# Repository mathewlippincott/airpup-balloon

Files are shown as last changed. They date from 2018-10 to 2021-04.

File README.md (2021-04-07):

# the Airpup kite balloon
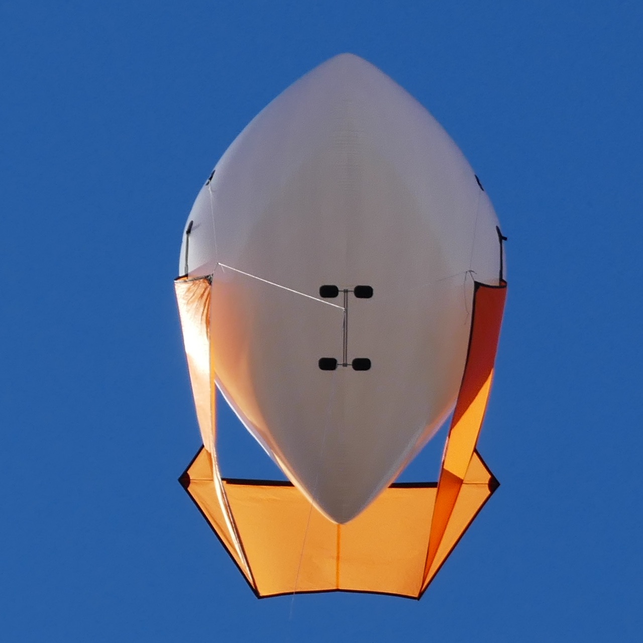
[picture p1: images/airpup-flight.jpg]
Airpup in flight
 

This repository contains the 2D patterns for constructing [Airpup](https://headfullofair.com/tags/airpup) as well as a corresponding 3D model. 2D patterns are made with [QCAD](https://qcad.org), the 3D model was made in Audodesk's Fusion 360.

See more of my kite and balloon projects at [headfullofair.com](https://headfullofair.com).

### files

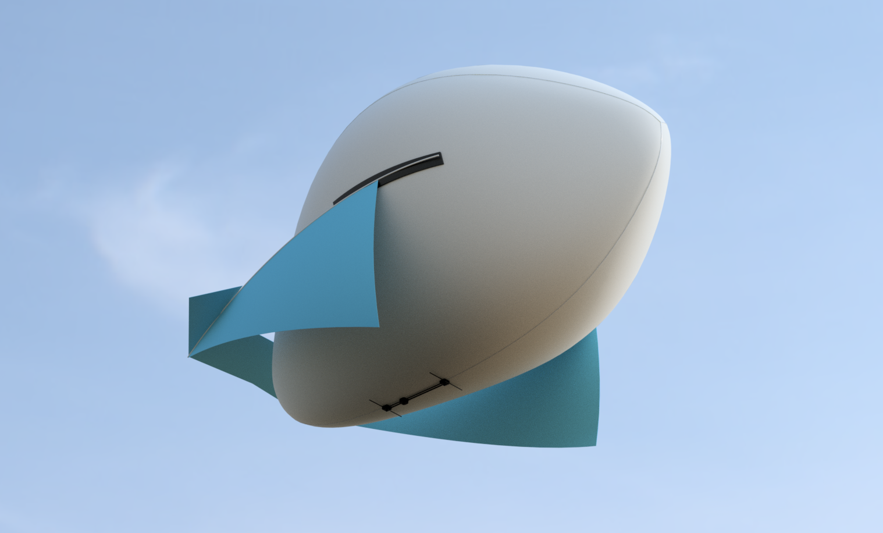
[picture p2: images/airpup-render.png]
rendering of airpup


* [/rails](rails), *belly mounting rails and STLs*
* BOM.ods, *Bill of Materials*
* V3-FIN.DXF, *panel diagram of the fin/wing structure and attachment*
* V3-ENVELOPE.DXF, *flat pattern of the balloon envelope*
* 72in-Airpup-model-v3.f3z/step/iges, *full-size 3D Airpup- Envelope is accurate in size, volume, and seam locations, fins are illustrative.*

Fin and envelope flat patterns have a series of rounded-rectanges that correspond to the glued interconnections joining the sewn fins and envelope. 

### sewing assembly
[airpup-assembly.md](airpup-assembly.md) contains instructions on sewing Airpup. 

### envelope construction

The envelope is a 3-gore pattern seamed in a single run:

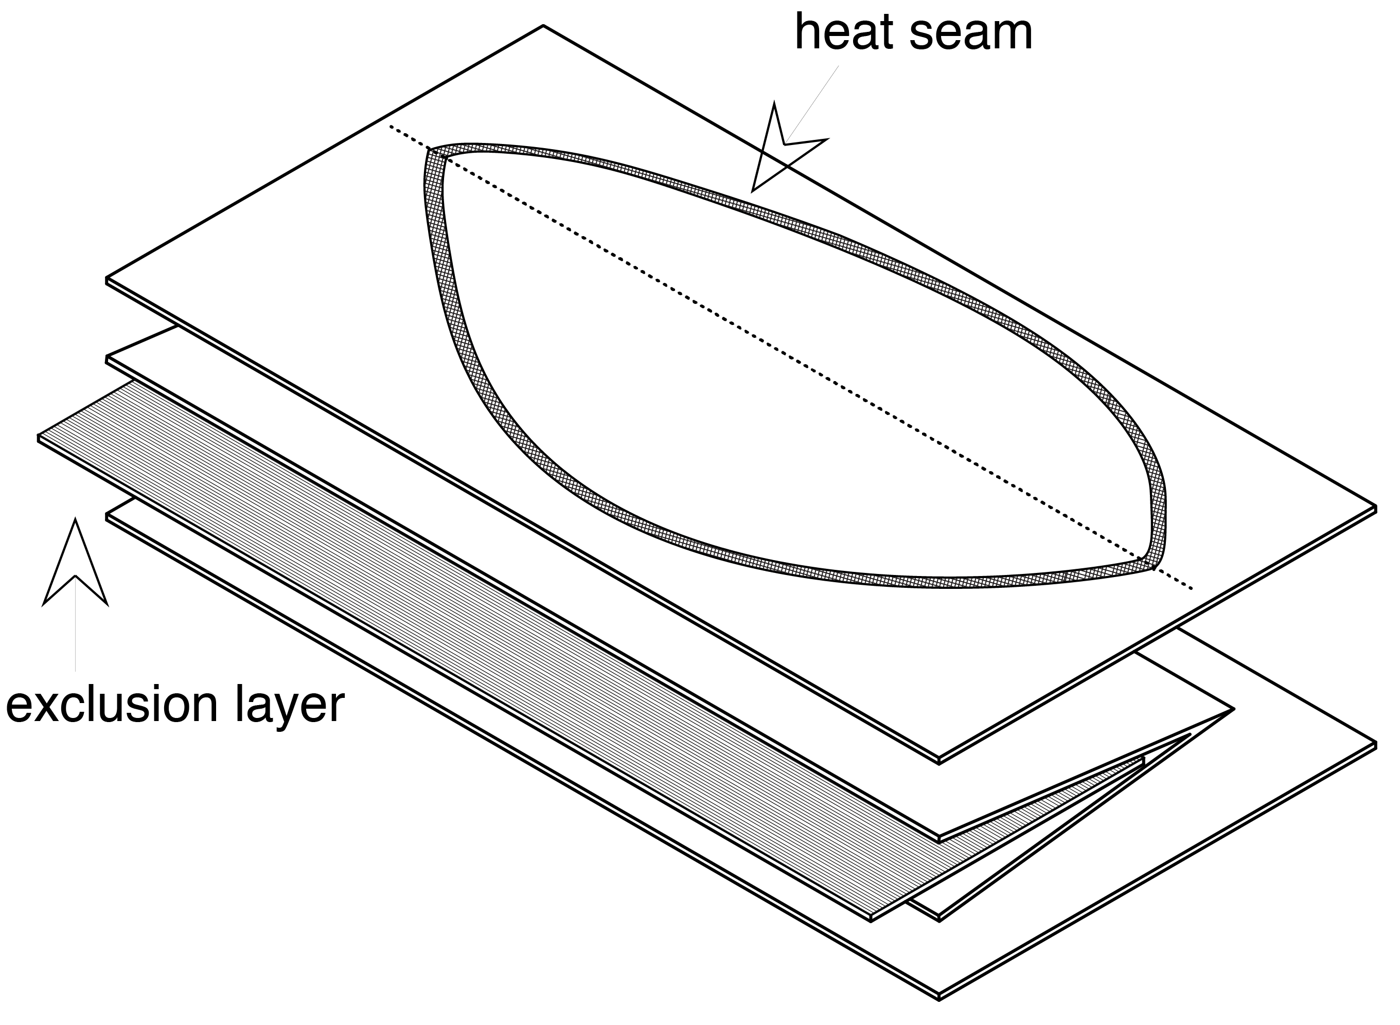
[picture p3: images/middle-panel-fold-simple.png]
pattern fold


### envelope volume and flat patterns

Airpup's envelope volume is roughly equivalent to a sphere whose radius is 1/3 the length of an inflated Airpup.

Airpup's flat envelope pattern is 1.147 times the length of an inflated Airpup.

### mounting rails
The folder [/rails](rails) contains CAD files and STLs for end caps and two-part slide mount. This mount allows easy weight adjustment and also can be removed from the belly of the balloon through four patches
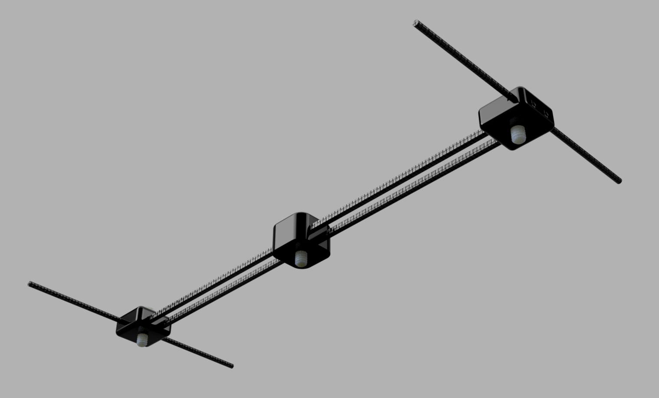
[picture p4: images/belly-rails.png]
The belly mount has a sliding rail system for easy adjustment


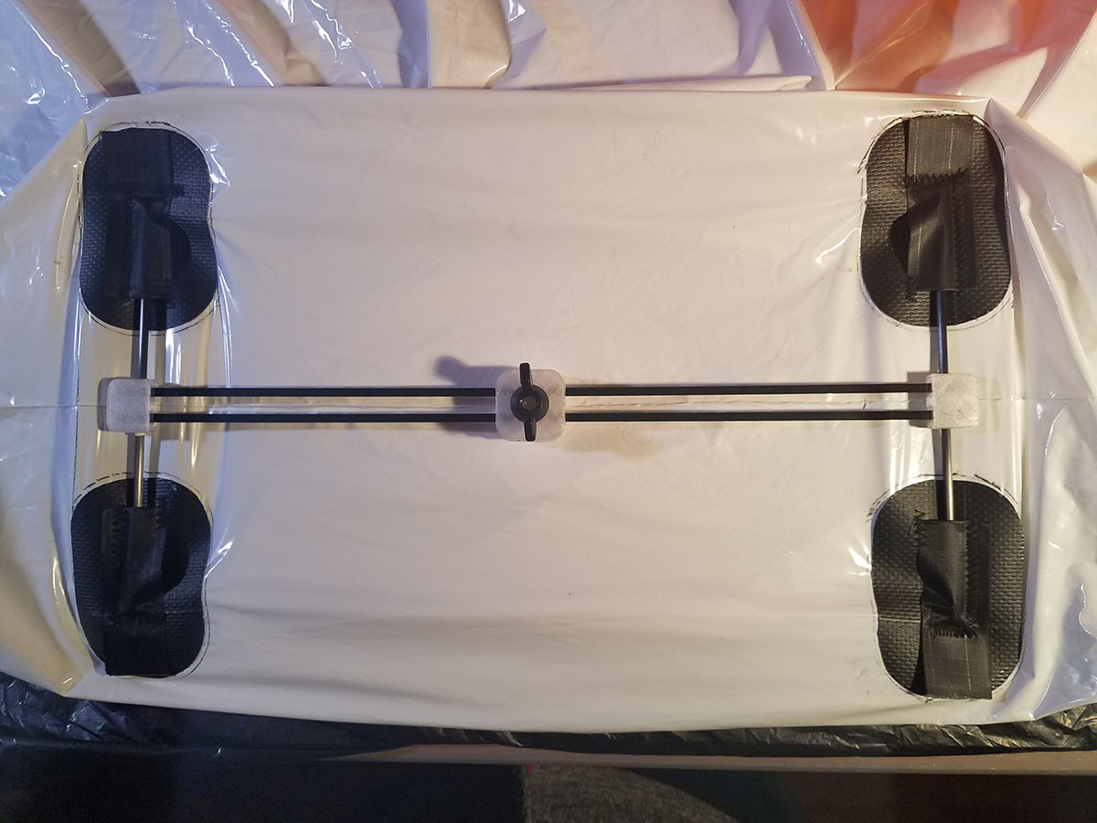
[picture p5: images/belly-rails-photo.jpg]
the rails allow quick weight adjustment


### contribute

* Use the 3D models to plan your payload attachement. Please [reach out](https://headfullofair.com/contact) and share.
* Fork this repository and improve the design or documentation.
* Add or comment on [issues in this repository](https://github.com/mathewlippincott/airpup-balloon/issues).
* [show me](https://headfullofair.com/contact) kite and balloon stuff.

All contributors are asked to abide by the [code of conduct](codeofconduct.md).

*Licensed under the [CERN OHL 1.2](license.md)*.

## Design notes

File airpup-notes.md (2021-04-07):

# Airpup Notes

## Safety
Airpup is a kite. Exercise safety guidance and judgement appropriate to kites. Avoid flying when lightning threatens or near power lines. Always check the weather before flying. Airpup cannot be safely handled in winds exceeding 20 miles per hour (32 kilometers per hour).

## Preflight Setup: adjusting angle of attack
Before flying, ensure Airpup's nose is pointed upwards, either by balancing the payload on belly rails or by adjusting the bridle (see below). The spars along Airpup's sides should be inclined approximately 15 degrees or more before taking to the air.

Failure to set upward angle of attack will result in unstable and potentially hazardous flight behavior. 

## Bridle adjustment
Your Airpup is rigged to fly with a payload on the belly. If you do not intend to mount a payload on the belly, the bridle must be adjusted.

The bridle is modular and has preset knots for setting an appropriate angle of attack without a belly-mounted payload. Remove the 10.5" strings from the rear legs of the bridle and shorten the front leg of the bridle to the upper knot.

## Inflation and deflation
Always use a balloon regulator to fill Airpup through the small nozzle. Approximately 37 cubic feet of gas will provide a complete fill. Upon filling, the balloon skin will be taught and the belly seam's wrinkles behind the payload mount will smooth out.

To empty Airpup, pull the dump valve.

Do not blow into Airpup with your breath! Moisture can degrade the balloon. A high-volume pump (such as for inflatable boats) or inflatable mattress pump are the best choices for air filling.

## Inserting Spars
For your convenience, the side spars are pre-installed on Airpup, and one side of the three-part transverse spar has been installed for demonstration purposes.

Before flying, ensure that all spars are together and snuggly within their pockets.

## Payload specifications
Airpup can lift approximately 600 grams fully inflated, and even more with wind assistance; however, a 500g or smaller payload is recommended.

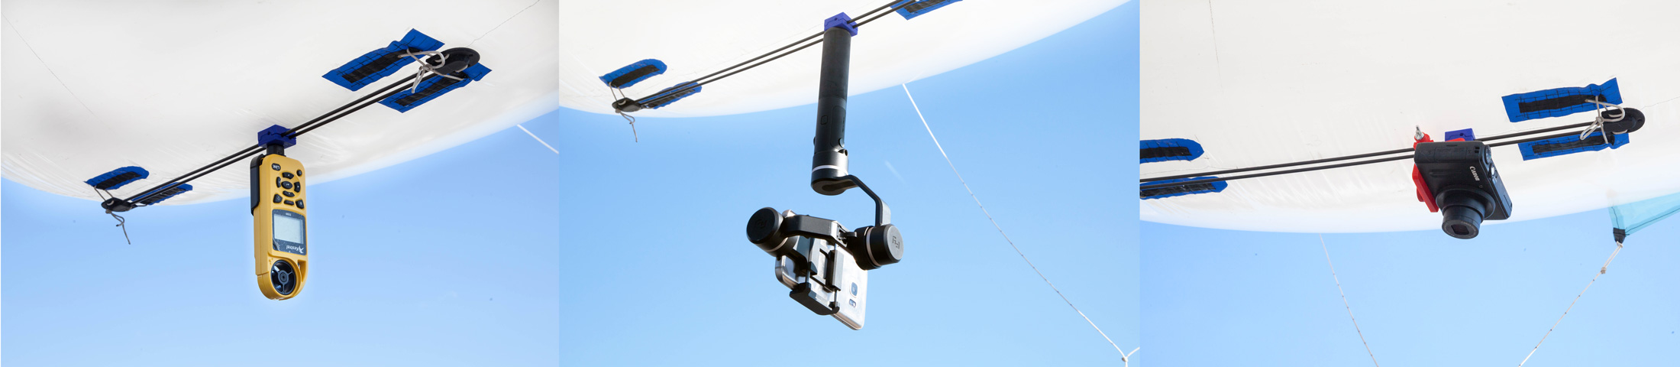
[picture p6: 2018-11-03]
images/airpup-config-wide.jpg

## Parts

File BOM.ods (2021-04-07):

Component | Material | Quantity | Unit
Envelope | 2 mil TPU | 1 | 1
Longitudinal Spars | 1/8” pultruded CFRP, 0.240 oz/yard | 2 | 60”
Transverse Spar | 1/8” pultruded CFRP, 0.240 oz/yard | 3 | 16.5
Ferrules | stainless steel, 1.5” long, OD .147”, ID .127” | 4 | 1.5”
vinyl end caps | 0.19” ID flexible PVC end cap | 6 | .5” long
Ripstop | 0.65 oz ripstop polyester | 2 | 60” x 36” (one yard)
Payload Rails | 1/8” square pultruded CFRP 0.49oz/48” | 2 | 12”
Payload transverse rails | 1/8” pultruded CFRP, 0.240 oz/yard | 2 | 6”
Pockets and Attachments | 1.5oz ripstop ribbon | 6.5 | 1” x 36”
Mounting Patches | V-10 coated vinyl (nylon reinforced) | 0.06 | 58” x 36”
Thread | Gutermann thread | 0.075 | 547 yard spool
Payload bolts | Nylon 7/16” hex head bolt, ¾” long 1/4-20 | 3 | McMaster #91970A540
wingnut | Nylon wing nut, 1/4-20 | 3 | McMaster #94924A600

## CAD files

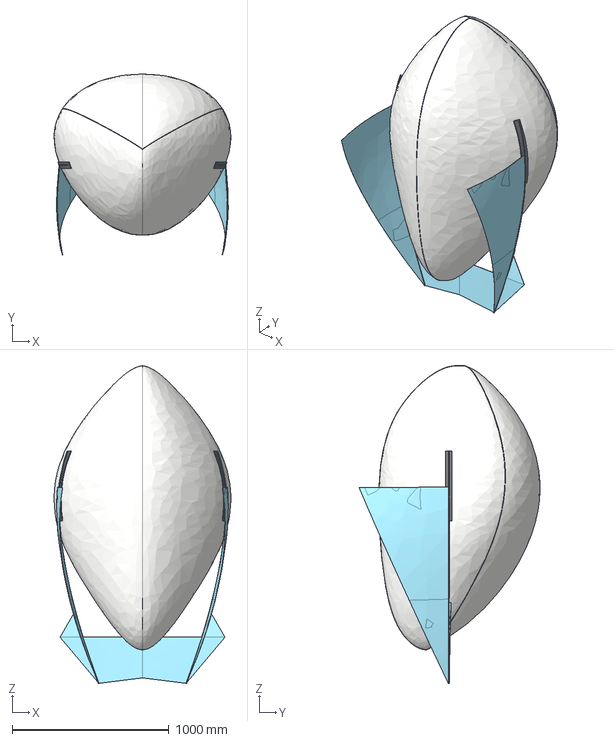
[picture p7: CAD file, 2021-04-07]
72-in-airpup-model-v3.step
1127.0 x 1153.3 x 2026.5 mm

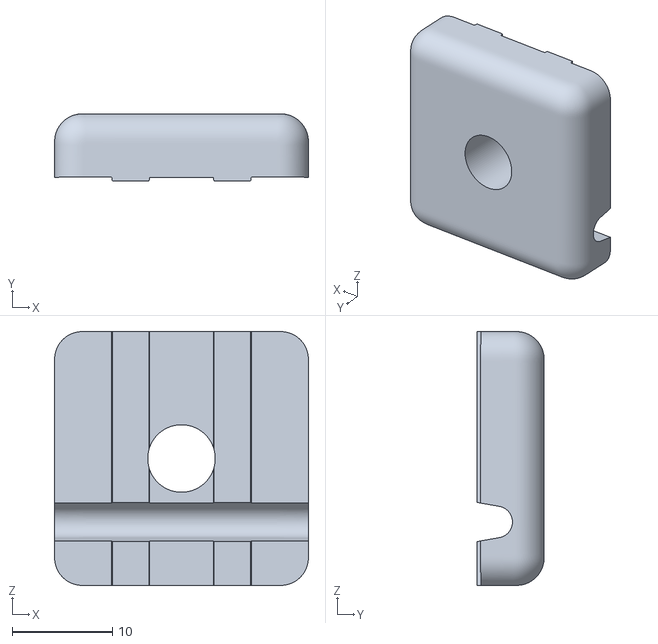
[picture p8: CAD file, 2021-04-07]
rails/square/endcap top.stl
25.4 x 6.75 x 25.4

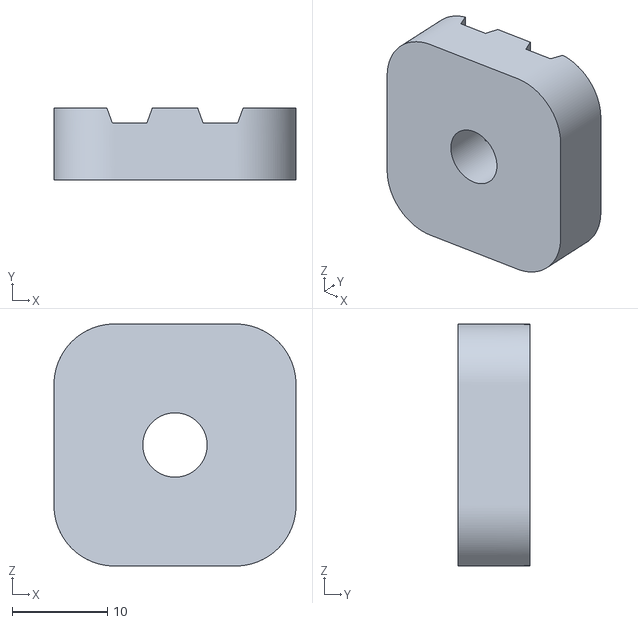
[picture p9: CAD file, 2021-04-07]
rails/square/bottom.stl
25.4 x 7.54 x 25.4

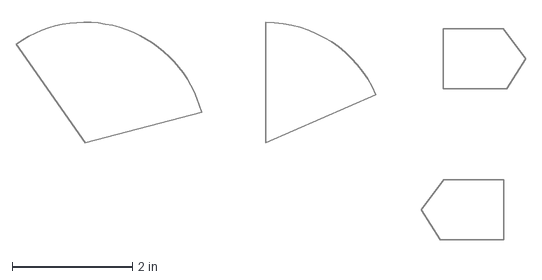
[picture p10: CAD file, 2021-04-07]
reinforcements.dxf
8.48 x 3.72 in

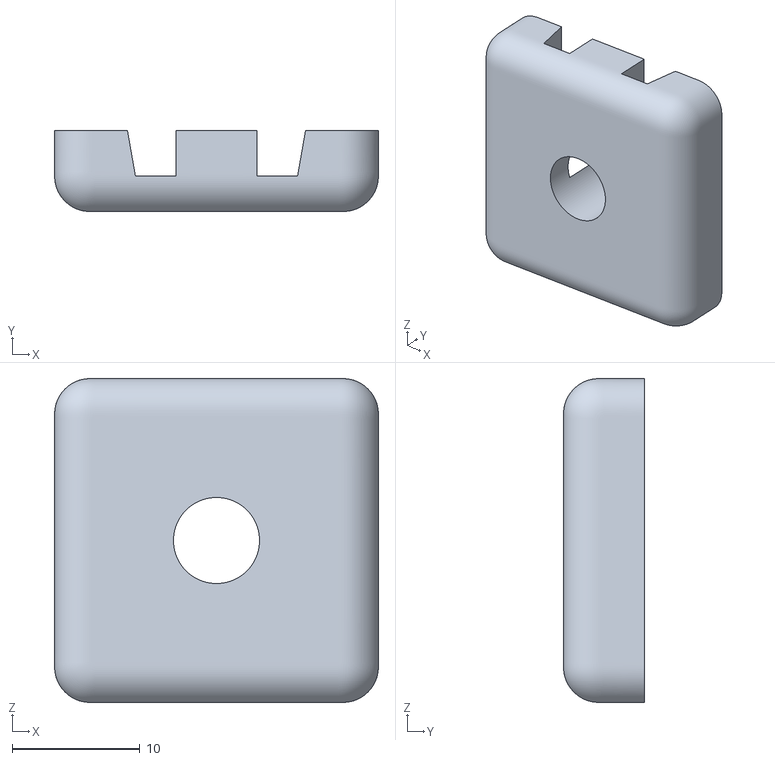
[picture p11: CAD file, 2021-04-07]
rails/square/endcap bottom.stl
25.4 x 6.37 x 25.4

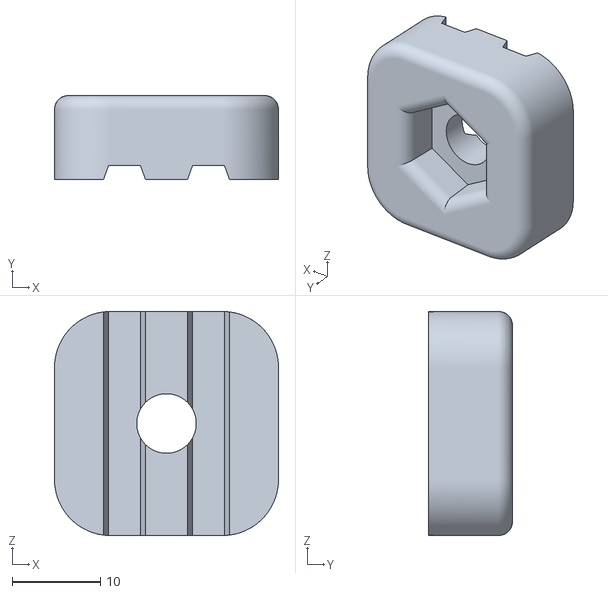
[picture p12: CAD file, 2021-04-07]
rails/square/top.stl
25.4 x 9.52 x 25.4

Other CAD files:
v3-FIN-2.dxf
v3-ENVELOPE.DXF
V2-FIN.dxf
v2-ENVELOPE.DXF
72-in-airpup-model-v3.iges

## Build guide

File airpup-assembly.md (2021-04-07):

## Components:

* Ripstop Polyester Panels (0.6oz)
   * __2x__ Wing Panels
    * __2x__ Winglets
    * __2x__ Keels
* 1-inch Ripstop Nylon Ribbon components(1.75oz)
	 * __2x__ Winglet Pockets
	 * __2x__ Keel Pockets
	 * All edge binding
* 2-inch Ripstop Nylon Ribbon (1.75oz)
	 * __2x__ Wing Pocket (has Gluing Patch sewn in center)
	 * __2x__ Winglet Reinforcements
	 * __4x__ Keel Reinforcements
* Fiberglass Reinforced PVC
	 * __6x__ Gluing Patches for attachment to the ballon envelope
    Grosgrain Ribbon
	 * __2x__ Bridle Loops

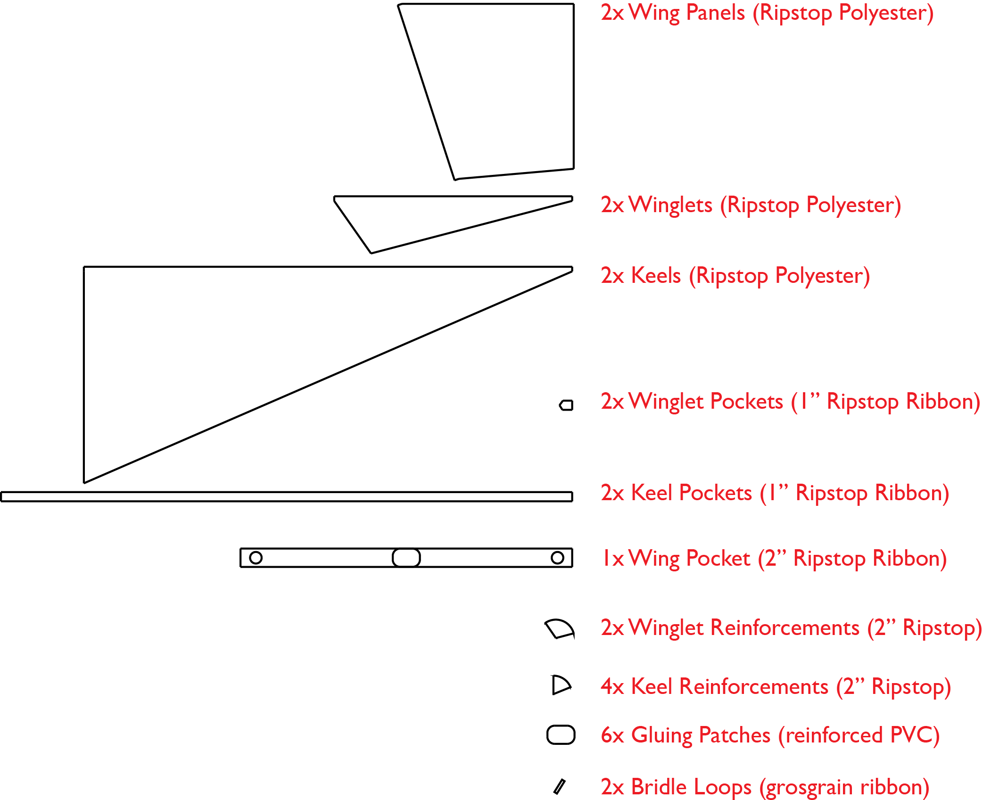
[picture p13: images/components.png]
components


## Assembly 

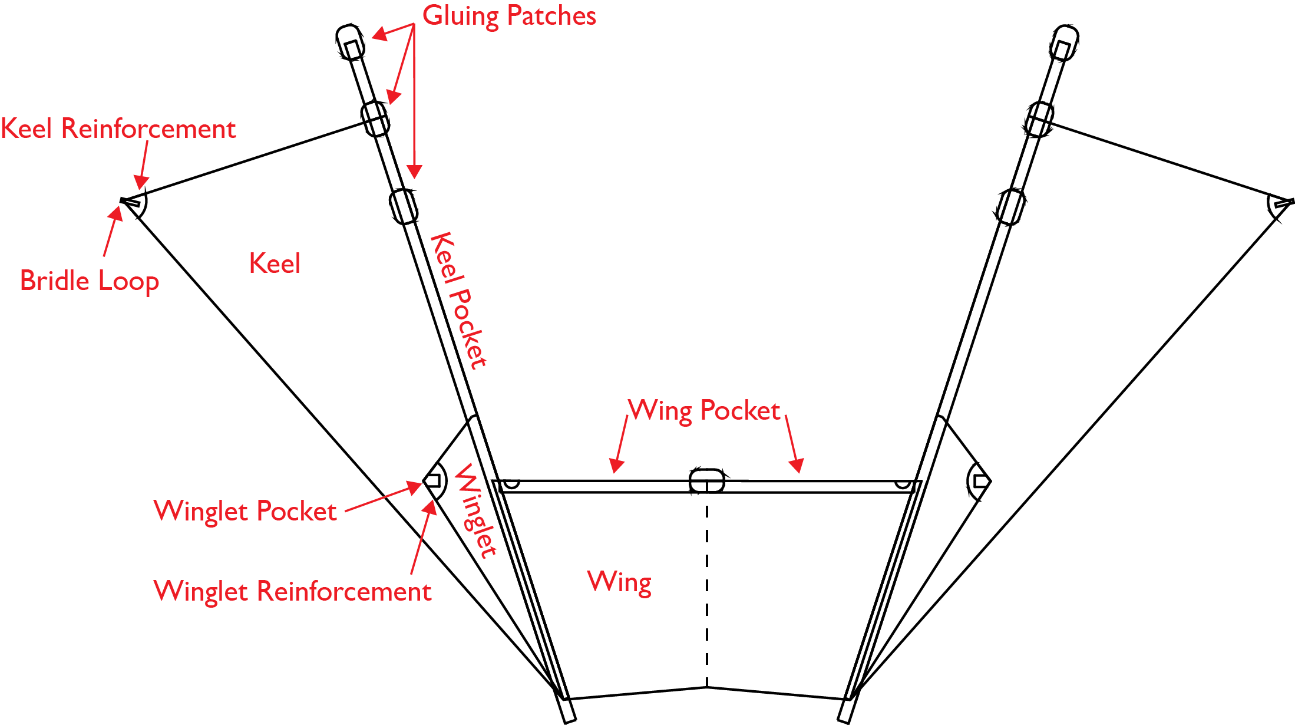
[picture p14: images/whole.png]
the whole sewn component


The fin structure of Airpup is assembled as individual panels which are then joined by edge binding along the length of the Keel Pockets.

Most stitches are a 3mmx3mm zigzag stitch, unless specified. 

### Keels
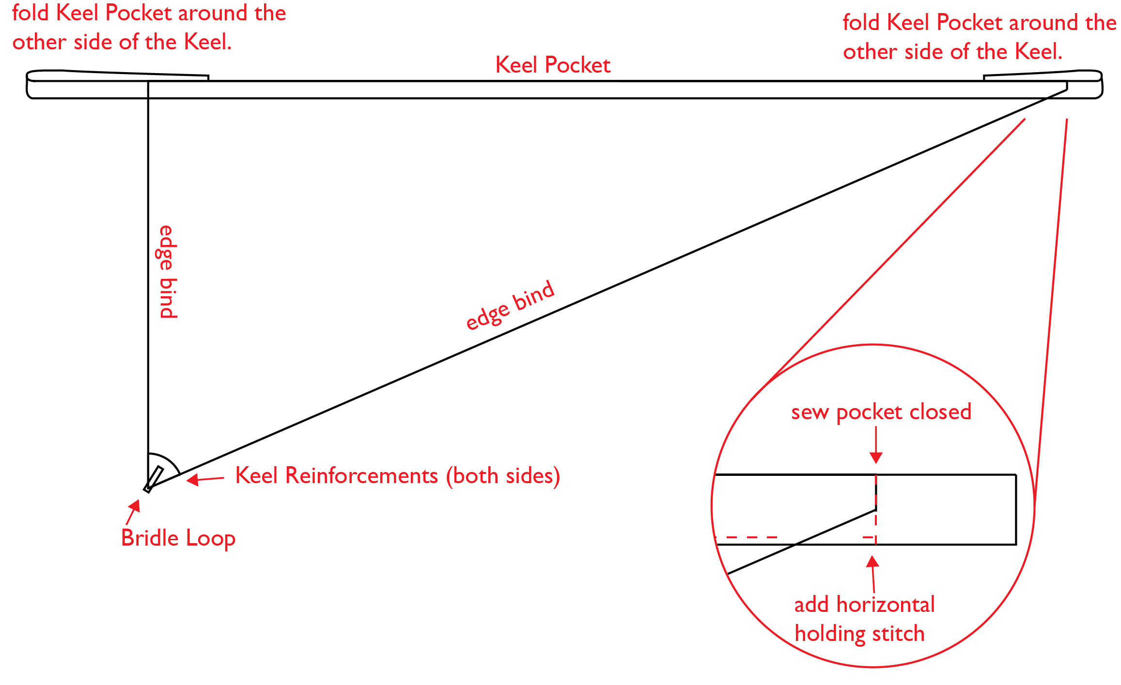
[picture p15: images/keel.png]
keels


2. Tack Keel Reinforcements to both sides of Keel tips.
3. Edge bind two exposed sides of Keel and Winglet.
7. Sew Bridle Loops to Keels.
8. Tack Keel Pockets to Keels, wrapping folded ends of Keel Pockets around to the inside of the Keels.
9. Sew Keel Pocket Closed with a vertical straight stitch, curving to a horizontal hold stitch. Reverse to double stitch.
10. Sew bottom of Keel pocket to Keel, leaving 1/8" margin and 1 1/4" gap for Pocket entry.

### Winglets
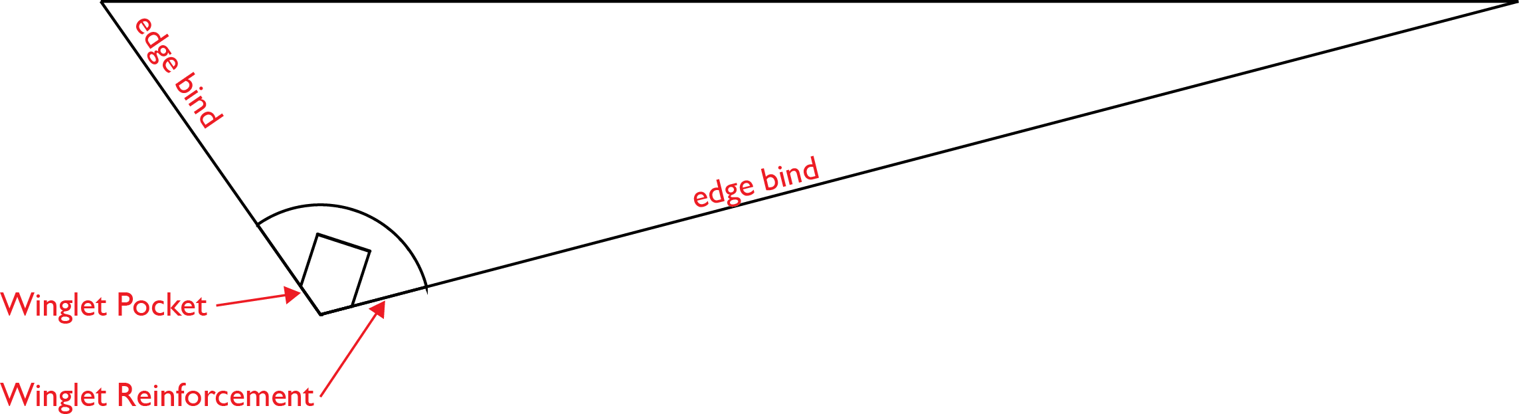
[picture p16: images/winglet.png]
winglet


1. Tack Winglet Pockets and Reinforcements to one side of Winglet's tips.
3. Edge bind two exposed sides of Keel and Winglet.
4. Sew sides of Winglet Pockets in place.
5. Sew Winglet Reinforcements in place.

### Wing
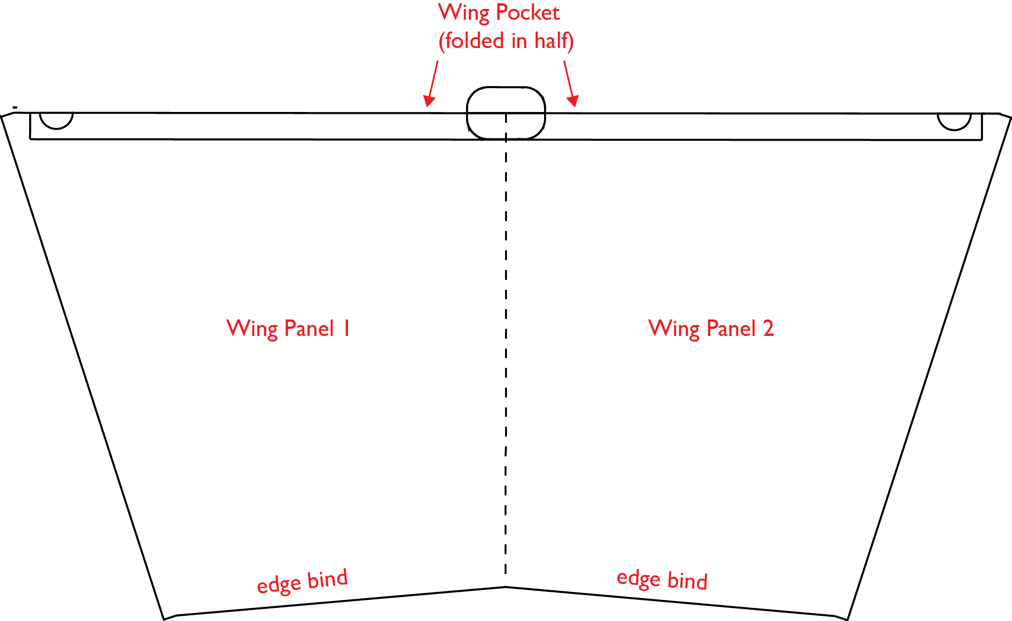
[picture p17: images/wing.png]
wing


1. Tack Wing panels together with seam tape and stitch.
2. Tape Wing Pocket in place, folded in half over the front edge of Wing. Tape in place with masking tape, then stitch, leaving a 1/2" wide pocket.
3. edge bind the back edge of the Wing.

### Combining Panels and Finishing
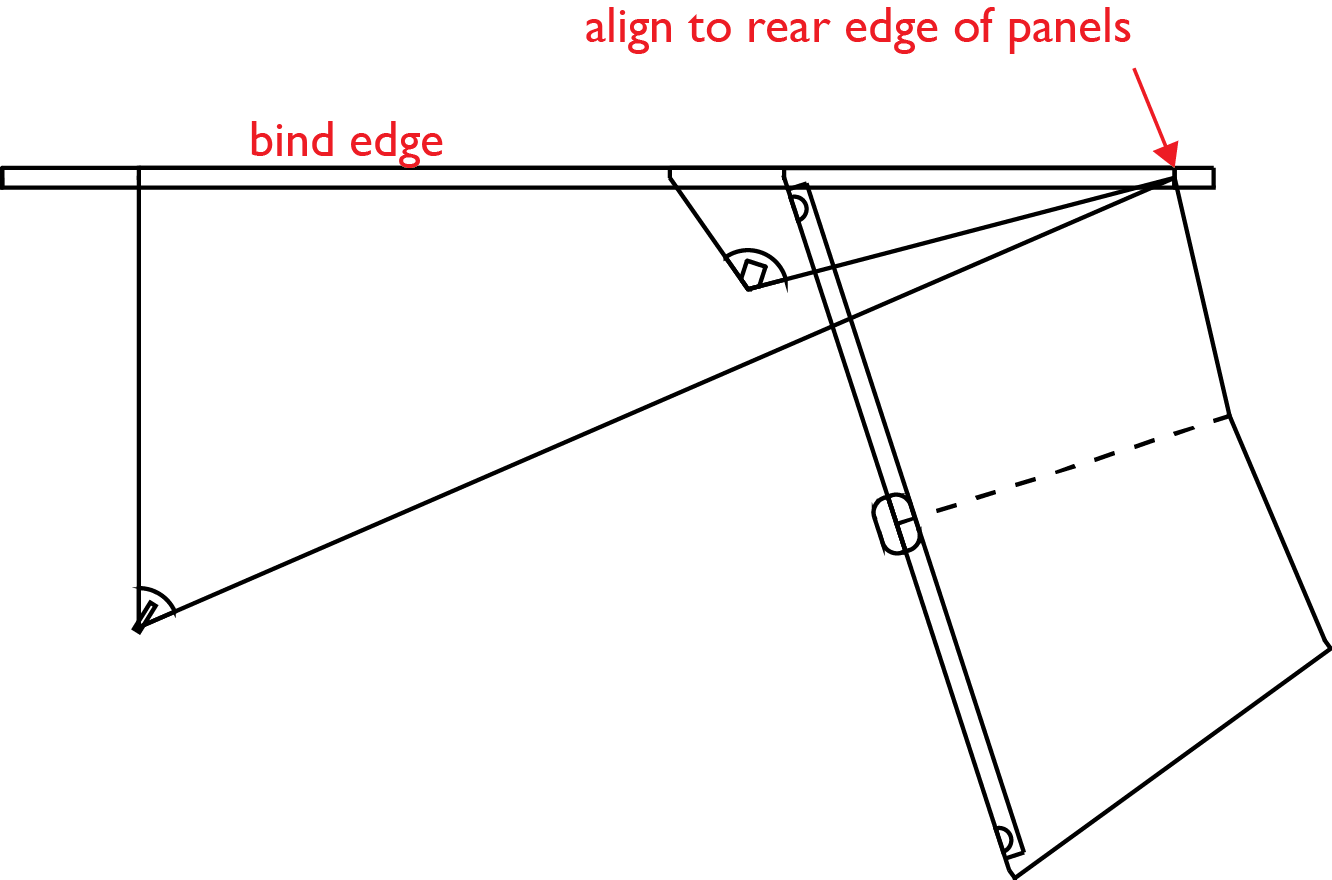
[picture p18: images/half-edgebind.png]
half-edgebind


1. Align Wing, Keel, and Winglet, to the back corner of the ripstop polyester panels. Tack together. Edge bind together.
2. Align other Keel and Winglet with Wing, aligning to back corner.
2. Mark locations of Gluing Patches with alignment tool and tape in place with masking tape. Check symmetry of the two sides and adjust Gluing Patches if necessary.
3. Sew Gluing Patches along 2" marked center, sewing to the edge-bound section and along the bottom of the pocket.

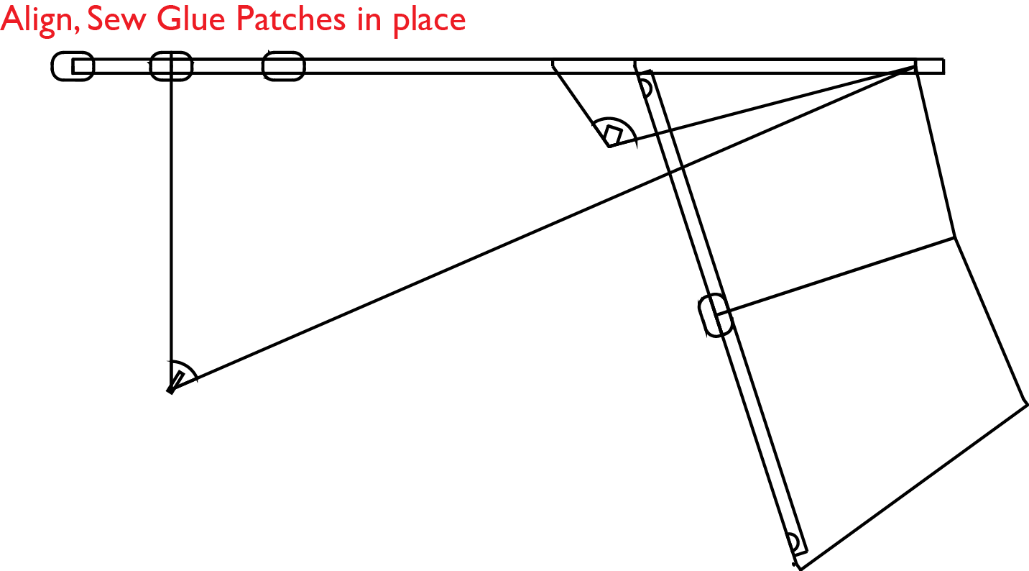
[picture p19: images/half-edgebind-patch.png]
half-edgebind
 

### Grouping Assembly Tasks
The assembly is easier to perform if edge binding and other tasks are grouped. This is my suggested order.

1. Tack Winglet Pockets and Winglet Reinforcements to one side of Winglets tips.

2. Tack Keel Reinforcements to both sides of Keel tips.

3. Edge bind two exposed sides of Keel and Winglet.

4. Edge bind back edge of Wing.

6. Sew Keel Reinforcements to Keels.

7. Sew Bridle Loops to Keels.

8. Tack and sew Keel Pocket to Keel.

8. Sew Wing Pocket onto front edge of Wing.

9. Align one edge of Keel, Winglet, and Wing to the back corner of polyester panels.

10. Tack together Keel, Winglet, Wing, and Keel Pocket.

11. Edge bind.

12. Align other side of Keel, Winglet, Wing and Keel Pocket, aligning to back corner.

13. Edge Bind.

15. Use alignment tool to identify Gluing Patch locations.

16. Tape Gluing Patches in place, sew into location.

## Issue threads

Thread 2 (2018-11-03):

Replace belly rails with square-profile rods

mathewlippincott, 2018-11-03:
Replace the belly rails with square-profile 1/8" diameter rods.

mathewlippincott, 2019-04-05:
take 1, successful print:
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

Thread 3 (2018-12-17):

Design belly patches for square-profile rods

mathewlippincott, 2018-12-17:
Belly patches that allow the square-profile rods and H-shaped support rods to be inserted, removed, and tightened in place.

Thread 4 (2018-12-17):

Smooth out panel intersection at the nose

mathewlippincott, 2018-12-17:
Airpup's nose intersection has a slight divot that needs to be removed. This divot lowers airpup's nose and makes it somewhat fin-like, which is undesireable. It is a by-product of scaling the envelope and changes in material stretch related to scale.

v2-ENVELOPE.DXF should fix this issue, but a new envelope is needed to verify.

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

mathewlippincott, 2019-04-05:
Revised [v2 envelope](https://github.com/mathewlippincott/airpup-balloon/blob/master/v2-ENVELOPE.DXF) has repaired the nose divot:
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

Closed 2019-04-05.

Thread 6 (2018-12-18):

Replace transverse spar's end caps with velcro attachments

mathewlippincott, 2018-12-18:
The transverse spar is held in place with end caps that should be replaced with velcro for easier insertion and stronger fabrication.

mathewlippincott, 2019-04-05:
Instead of velcro, there will be riveted connectors from [Prism.]
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

mathewlippincott, 2021-04-07:
Used a pocket instead

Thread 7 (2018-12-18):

Sew wing spar pouch to envelope attachment patch at top and bottm

mathewlippincott, 2018-12-18:
Currently only the top of the wing spar pouch is sewn to the envelope attachment patch.  Change the assembly so that the wing spar pouch is securely sewn at the top and bottom.

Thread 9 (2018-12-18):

Re-design transverse spar envelope attachment patch

mathewlippincott, 2018-12-18:
The current prototype's attachment patch is a hodge-podge because of multiple iterations and a lack of space. It should be cleaner.

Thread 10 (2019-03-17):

publish cad files in open format

Olm-e, 2019-03-17:
hi,
now the cad files are published in closed format (dxf -late version-  and fusion 360) impossible to use on a free operating system and difficult to work with or export to other software

stl are fine as well as svg and other open format

would it be possible that you export them and work with open format ?
thanks a lot !
(planning to roll my own small scale version, actually wondering if not worth to redo it all instead of spending time on file export hunt... ;) )

mathewlippincott, 2019-04-05:
Olm-e,
I do my best to use open source programs, and all the 2D CAD files are created in [QCAD](http://qcad.org/), which is F/OSS. I can do an SVG export as well, however I have to work in inches due to my factory relationship, and that makes SVGs a poor working format.

The STEP and IGES versions of the 3D files are the preferred cross-platform files. You should be able to open them in Blender or other 3D programs.

mathewlippincott, 2019-04-05:
@Olm-e STLs have been available for all 3D printed components as well.

Closed 2019-04-05.

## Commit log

2018-10-16 Populated repository
    [72in-Airpup-model-v1.step, BOM.ods, V2-FIN.dxf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]
2018-11-03 Updated all models with belly mounting rails + stls and renderings
    [72_Airpup-model-v1.iges, 72_Airpup-model-v1.step, 72in-Airpup-model-v1.step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]
2018-11-03 added rails image
2018-11-03 #2 take 1 of square rails
    [94613A540bolt.stl, square belly mount v3.f3d, square-end-cap.stl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]
2018-12-18 #2 updated .stl files so that they are in mm rather than inches
    The CAD files are done in inches in order to match the dimensions of attachment hardware but 3D printed files should be in mm to avoid issues.
    [94613A540bolt.stl, square-end-cap.stl, square-slider-mount-bottom.stl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]
2018-12-18 revised square belly mount components based on 3D print test #2
    [square belly mount v3.f3d, square belly mount v8.f3d, square-end-cap.stl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]
2021-04-07 Airpup V3 (production version) update
    update to all components of the full Airpup V3 assembly
    [72-in-airpup-model-v3.iges, 72-in-airpup-model-v3.step, 72_Airpup-model-v1.iges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]
